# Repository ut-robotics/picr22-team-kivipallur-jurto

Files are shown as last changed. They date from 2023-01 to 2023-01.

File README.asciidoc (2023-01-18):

# Kivipallur-Jurto

Team members: +
Artur Reitalu +
Kristjan Madis Kask +
Kaspar Tamm +
Priit Teelahk +

== Fusion 360 Kivipallur Jürto
https://a360.co/3hoEI0K

== External links
Fusion 360 CAD - https://www.autodesk.com/products/fusion-360/overview?term=1-YEAR&tab=subscription +
Remmina - https://remmina.org/ +
Altium PCB Design - https://www.altium.com/ +
VNC Viewer/Server - https://www.realvnc.com/en/connect/download/viewer/ +
OpenSSH - https://www.openssh.com/ +

# Electronics
Compared to the beginning of the course, we reduced the electronics to a smaller size. On the new mainboard motor drivers and control logic are combined to one PCB. The new board has the option of adding more motors to add more functionality to the robot. It is easier to manage cables on the new board

The first fix to do is to add LEDs to the motor drivers. Another improvement is to buy new and better handling motor drivers for the course.

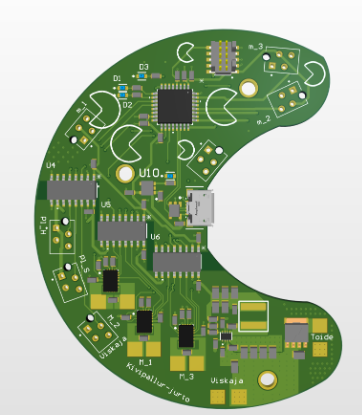
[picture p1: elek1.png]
Board1


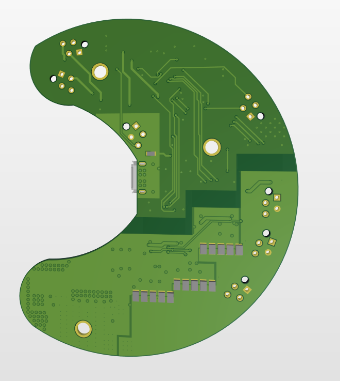
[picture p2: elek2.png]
Board2


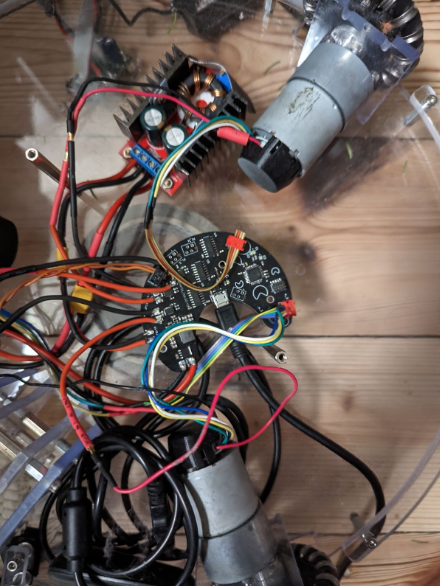
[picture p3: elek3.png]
Board3


# Mechanics

3d-printed battery and alarm holders for the robot for better fit and alarm stability. To add a little character to our robot, we added 3d-printed Kivipallur Jürto face to the camera holder. We also added some borders to sides and back to ensure that the ball will not get stuck outside or inside of the robot. We created 3d-printed borders to thrower, that guide the ball correctly. Moved most of the cables inside of the robot. +
Our ball thrower has a fixed throwing angle of 60 degrees. Distance between thrower sides is 42 mm, The distance between motor and ball slider ramps is 35 mm and the distance from motor to the ground is 38 mm. The sliders have cutouts for support and stability, as they sit on the bottom plate. +
Photos of our robot. +

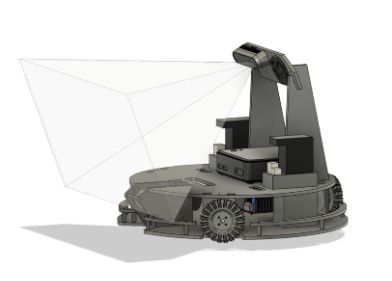
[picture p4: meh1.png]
robot1


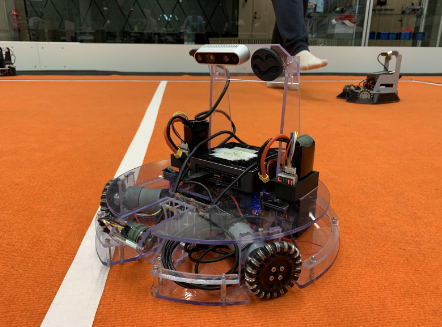
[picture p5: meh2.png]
robot2


Significant improvements can be achieved with smaller bottom and top plates. The robot did not do great in corners because of its big dimensions. Thrower clearance should be higher, because it would get stuck on some uneven surfaces. It’s more efficient to design the ball thrower with a ball holder and changeable angle, rather than a simple one. Otherwise everything worked perfectly and our robot was an improvement from the previous one. 

# Software

## Used libraries:

### OpenCV - https://opencv.org/ +
	Opencv is used for the image processing functions and object detection through contours.
  
### NumPy - https://numpy.org/ +
	Numpy allowed us to have and use more complex array processing functions for line detection.
  
### Xbox360controller - https://pypi.org/project/xbox360controller/ +
	Xbox360controller library was used solely for reading Xbox 360 controller inputs.

### Numba - https://numba.pydata.org/ +
	From the Numba library we used the JIT functions,which allowed us to speed up nested loops.

### WebSocket(Client) - https://pypi.org/project/websocket-client/ +
	Websocket client was used to actually connect to the referee server.

### Pyserial - https://pypi.org/project/pyserial/ +
	Pyserial was used to comfortably receive and send commands to the microprocessor which controlled the motors.

### Pyrealsense2 - https://pypi.org/project/pyrealsense2/ +
	Pyrealsense2 gave us the tools needed to use the camera feed from our intel realsense camera to its full potential.

### Multiprocessing - https://docs.python.org/3/library/multiprocessing.html +
	Multiprocessing is used as an alternative for multithreading, since it is supposed to be more effective.
	
### Pickle and segment + 
	Pickle and segment libraries were also used but they came with the bootcamp code, and pickle serialized objects and segment made color thresholding easier.

## Code structure

There were 4 main components in our code: +

* state machine
* referee listener
* omnimotion processor
* image processor

The state machine cycled through certain states (which are listed below), it was basically the coordinator on which functions to run and what to do with certain data from image processor. +

Referee listener was responsible for connecting to the referee server and constantly checking if there were new messages to forward to the state machine for it to change states and/or update basket color. +

OmniMotion processor converted basic forward and side ways movement in meters per second to correct maiboard units for the motors. +

Image processor is the component which analyzed camera frames and converted that info into ball, basket and line detetction

[horizontal]
Spin:: rotates to find a ball after about 1000 degrees of turning it goes into Enemy_basket_spin, if it found a ball before the goes into drive state.
Drive:: drives towards a found ball and stops after getting to certain range and goes into orbit state, if ball is lost during it goes back to spin state.
Orbit:: starts looking for the target basket while keeping the ball at the center of its camera(orbiting around ball), if ball is found goes into throw state, if ball is lost goes back into spin state.
Throw:: final lineup of ball and basket and starts the throw function, if ball is lost during this time goes back into spin state.
Controller:: if a connected controllers takeover button is pressed robot becomes controllable by controller until relinquish button is pressed.
Enemy_basket_spin:: state similar to spin but for the enemy basket, if found goes into enemy_basket_approach.
Enemy_basket_approach:: state to approach an enemy basket until a certain distance, if distance is reached goes back into spin state.

## Game logic
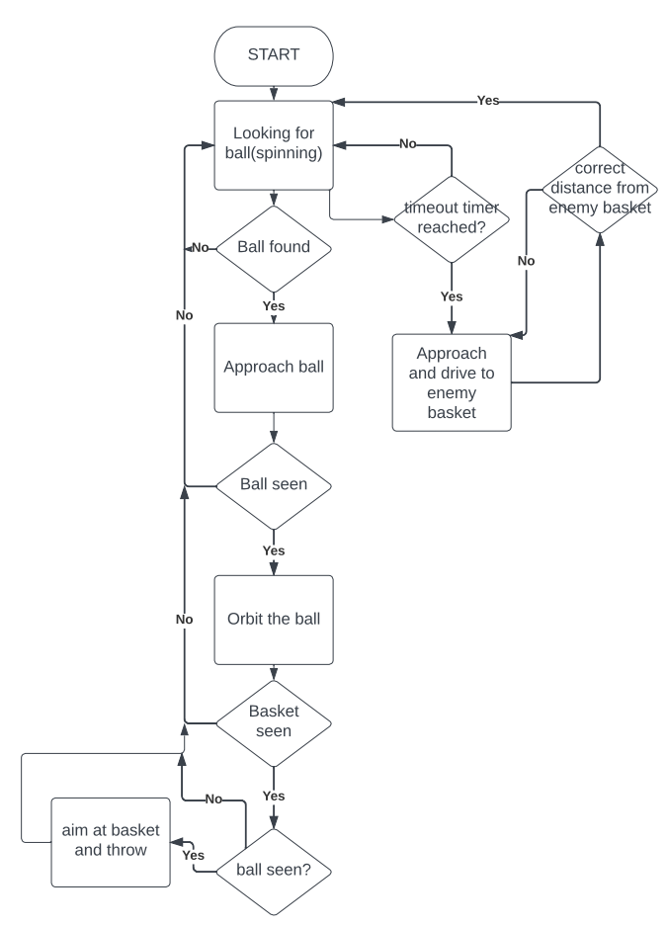
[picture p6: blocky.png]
blocky


## The Good, Bad and the ugly things i would change

### The GOOD +

I would say that the good things in our code were: numba jit which sped up our image processor and upped our frame rate by 10, controller integration which enabled our code to be able to be run without a referee server available and relatively more compact main.py then most.
	
### the BAD and the ugly i would change +

The worst thing about our code is that we don't measure our distance from object other than the basket which causes us to crash into other robots and the baskets backboard. Another bad thing is that our thrower speed calculation was linear which made it hard to throw in the balls. So i would change the depth camera usage to map out certain object if they are too close and execute countermeasures, and also remeasure our throwing distances and speeds.

# Personal comments

### Kaspar +
I worked on electronics design and assembly and wrote firmware for new electronics. I learned to use the Altium designer and STM32CubeIDE software. Next time I would do better to fix the schematic first before I start working on the PCB board. The collection of course materials is total chaos. The organization of the course has not been thought through. Next year's students, ask for advice from those who have passed already. Instructors must develop communication skills and the course schedule must be established before the course

### Artur +
I worked on the code together with Priit. I improved my code writing skills in python and also learnt about time management. Next time I would try to not reinvent the wheel (make everything by ourselves from scratch), but instead try to use more of what was available and already given to us (previous year’s code, instructors’ help, other teams’ help and their code examples). +
What I liked about the course was that it’s the only course (for us thus far at least) where you can earn money and you have creative freedom. +
What I did not like about the course was the lack of help, we got stuck on different tasks so often and it was super easy to burn out. We often just tried to fix one bug for several hours while with the instructors’ help it took only like 10 minutes to fix. The problem was that the instructors were available for only 2 lessons per week and then everybody needed their help, so there was a queue, who gets to ask them. Also the bi-weekly progress reports were extremely unnecessary and annoying in my opinion, as they just took away 25% of the sessions in which we could ask for the instructors’ help, instead we just had to watch and wait to get points. I don’t feel like it was motivating to move forward or make progress, but instead to just slow us down. +
Suggestion for next year’s students: Start early and don’t be scared to ask for help and use what has already been done for you. +
Suggestions for instructors: I understand that the current instructors work elsewhere and this course is like a part time job for them, but the students could really use more face-to-face consultations as slack communication is not very efficient and the in-person lessons always have such long queues to ask a question. + Maybe one more in-person lesson per week would ease the problem. +

### Madis +
I worked on the mechanics part of the robot. I learned to use Fusion 360 Autodesk software and how to design a functional robot from scratch. Learned how to use a mill and lathe. Next time I would look over my design a few more times to discover some mistakes I made. In this course I liked the idea of making all parts of the robot ourselves and getting a real functioning result. I didn’t like that sometimes I couldn’t continue my work, because I had to wait for supervision or the devices I had to use were in use. For future students I recommend starting early with everything and thoroughly thinking it through. For instructors I suggest to communicate more on slack, even if it's not so important, for example, if you haven’t supervised the work yet, but plan to do it in the next hours or day. It would be good to know all the issues right away, not each one with next feedback.

### Priit +
I worked together with Artur on the programmingof the robot. I learnt that cooperating with others while writing code is not always the best way, since we had many inconsistencies and problems. Next time i would definetly set out certain parts of the code i am responsible for and the other parts that my teammate is responsible for. The worst thing about the course was definetly the lack of lessons weekly which of some were completely gone for the progress presentation which actually dwarfed our progress i would say. Everything else in the course was great. Suggestions for other student would definetly be that try to complete the code and the robot by the 1st of December or even earlier, since building the new robot brings alot of new variables which could absolutely take all of your time away.
The instructors were very friendly and knowledgeable. There were some weird rules about formatting weekly reports, but other then that i have no personal quarrels.

== Blog

=== Sunday 2022-09-04

*Kaspar:* Soldered mainboard.  (2h) +
*Madis:* Assembled test robot. (1h) +

=== Wednesday 2022-09-07

*Priit:* Established a VNC Connection.  (2h) +
*Artur:* Helped with the VNC Connection.  (2h) +

=== Thursday 2022-09-08

*Kaspar:* Added heatshrink to cables. Connected a second powerswitch, which was missing.  (1.5h) +
*Priit:* Established communication with the mainboard.  (3.5h) +
*Artur:* Helped with Establishing a connection with the mainboard.  (3.5h) +

=== Monday 2022-09-12

*Madis:* Started designing the thrower. (5h) +
*Priit:* Attempted to establish a ssh connection, but didn t have much luck.  (2h) +
*Artur:* Also tried to get the ssh working to no avail.  (3.5h) +
*Kaspar:* Was writing an Estonian more throrough blog.  (1.5h) +

=== Thursday 2022-09-15

*Madis:* Finished designing the thrower. (5h) +
*Priit:* Got ssh working  (2h) +
*Artur:* Helped and celebrated getting ssh working.  (2h) +
*Kaspar:* Started doing the presentation.  (1.5h) +

=== Monday 2022-09-19

*Everyone except Madis:* Presented the presentation and listened to other teams. (3h) +

=== Thursday 2022-09-22

*Priit:* successfully opened the camera and tried different ways of detecting the balls. (4h) +
*Artur:* finsished the ball detection and we settled for the conture route (3h) +
*Kaspar:* Got Altium working and familiarised himself with the different components we could use.  (1.5h) +
*Madis:* Started with CAM, but ran into some problems with arrange (1h) +

=== Saturday 2022-09-24
*Madis:* Finished Fusion 360 CAM and waiting for supervision. (2h) +

=== Monday 2022-09-26

*Priit:* Helped with researching the code and main ball mover and carrier. (2h) +
*Artur:* Polished our ball detection software. Started developing the moving based on the closest balls x coordinate. (2h) +
*Kaspar:* Updated Project manager excel file, attached the NUC with screws to the test robot. Also photographed our accomplishments.  (2h) +

=== Wednesday 2022-09-28

*Artur:* Worked on robot movement. (2h) +

=== Thursday 2022-09-29
*Priit:* Broke the VNC Viewer tried different programs, but ended up back at VNC Viewer. (4h) +
*Kaspar:* Assisted with research on VNC Viewers. Worked on presentation slides, charged lipo batteries  (2h) +

=== Sunday 2022-10-02
*Priit:* reviewed the slides. (1h) +
*Kaspar:* reviewed the slides. (1h) +
*Artur:* reviewed the slides. (1h) +
*Madis:* reviewed the slides. (1h) +

=== Monday 2022-10-03
*Madis:* Resolved 2D Pocket and Contour issues with Fusion 360 CAM. Got positive feedback and milled the details. Presented the project status. (5h) +
*Priit:* Presented the project status. (1h) +
*Kaspar:* Presented the project status. (1h) +
*Artur:* Presented the project status. (1h) +

=== Thursday 2022-10-6
*Priit:* coded an alpha version of the code to track and follow the ball. (4h) +
*Artur:* helped to code and test the track and follow code.(2h) +
*Madis:* Modified robot and thrower, finally assembled thrower as well. (3h) +
*Kaspar:* Looking pcb components for Altium. (2h) + 

=== Friday 2022-10-7
*Kaspar:* Worked on motor driver and controller pcb schematic. (7h) +

=== Monday 2022-10-10
*Artur:* Worked on the robot motion program. (3h) +

=== Thursday 2022-10-13
*Priit:* Worked on the robot motion program and filmed robot moving in the field. (3h) +
*Kaspar:* Worked on slides and project plan, helped Priit debug the motion program. (3h) + 
*Madis:* Worked on the robot's wheel design. (3h) +

=== Sunday 2022-10-16
*Priit:* reviewed the slides. (1h) +
*Kaspar:* reviewed the slides. (1h) +
*Artur:* reviewed the slides. (1h) +
*Madis:* reviewed the slides. (1h) +

=== Monday 2022-10-17
*Priit:* Presented the project status. Did some coding. (4h) +
*Kaspar:* Presented the project status. Prepared the robot for the test robot presentation. (4h) +
*Artur:* Presented the project status. Did some coding. (4h) +
*Madis:* Presented the project status. Prepared the robot for the test robot presentation. (4h) +

=== Thursday 2022-10-20
*Madis:* Finished designing omniwheels and waiting for feedback. (4h) +

=== Friday 2022-10-21
*Madis:* Designed motor mounts and created assembly with omniwheel, motor holder and motor. (2h) +
*Kaspar:* Worked on motor driver and controller pcb schematic. (4h) +

=== Sunday 2022-10-23
*Artur:* Worked on the movement and image processing parts of the code. (3h) +
*Madis:* Fixed issues with motor mounts. (1h) +
*Kaspar:* Worked on motor driver and controller pcb schematic. (8h) +

=== Monday 2022-10-24
*Madis:* Used lathe to make three aluminum wheel-motor mounts. Next step is to clean them and drill holes. (4h) +
*Artur:* Improved our state machine code. (3h) +
*Priit:* Did some coding. (2h) +
*Kaspar:* Helped Priit with coding. (2h) +

=== Wednesday 2022-10-26
*Priit:* Struggled with classes and serial. (5h) +
*Madis:* Finished wheel-motor mounts. (2h) +
*Kaspar:* Experimented with the robot's ball throwing ability. (1h)+

=== Thursday 2022-10-27
*Priit:* Got the serial working and ironed out classes issue. (2h) +
*Artur:* Helped with debugging our issues. (2h) +

=== Friday 2022-10-28
*Priit:* Implemented primitive orbit and throwing functions. (4h) +
*Kaspar:* Worked on motor driver and controller pcb schematic. (4h) +
*Madis:* Started with camera holder design (2h) +

=== Saturday 2022-10-29
*Priit:* Improved orbit function. Also implemented depth camera distance. Fixed bugs (2h) +
*Kaspar:* Worked on motor driver and controller pcb schematic. (4h) +

=== Sunday 2022-10-30
*Priit:* reviewed the slides. (1h) +
*Madis:* reviewed the slides. (1h) +
*Artur:* reviewed the slides. (1h) +
*Kaspar:* reviewed the slides.Fixed feedback points and started pcb design (6h) +

=== Monday 2022-10-31
*Priit:* Presented the project status. (2h) +
*Kaspar:* Presented the project status. (2h) +
*Artur:* Presented the project status. (2h) +
*Madis:* Presented the project status. (2h) +

=== Thursday 2022-11-03
*Madis:* Designed new thrower. (3h) +
*Priit:* Developed a badly hardcoded throwing code. (3h) +
*Artur:* Worked on the robot program. (3h) +

=== Friday 2022-11-04
*Madis:* Started with new robot design (3h) +
*Kaspar:* Worked on pcb schematic and implemented suggested fixes (4h) +

=== Saturday 2022-11-05
*Kaspar:* Worked on pcb schematic and implemented suggested fixes (5h) +

=== Sunday 2022-11-06
*Madis:* Designed new robot upper plate and started to assemble new robot in Autocad (2h) +
*Kaspar:* Worked on pcb schematic and implemented suggested fixes (4h) +

=== Monday 2022-11-07
*Priit:* Fixed the hardcoded throwing code and added plastic fangs to help ball alignment (2h) +
*Kaspar:* Helped test the robot's ball throwing (2h) +
*Artur:* Improved new code. (2h) +

=== Tuesday 2022-11-08
*Madis:* Designed new robot. Added borders to bottom plate. (2h) +

=== Thursday 2022-11-10
*Priit:* Participated in the first test competition (5h) +
*Madis:* Participated in the first test competition (5h) +
*Artur:* Participated in the first test competition (5h) +
*Kaspar:* Participated in the first test competition (5h) +

=== Friday 2022-11-11
*Kaspar:* Fixed feedback points and started pcb design (3h) +

=== Saturday 2022-11-12
*Kaspar:* Received schematic feedback and finalized the new component placement (4h)

=== Sunday 2022-11-13
*Priit:* reviewed the slides. (1h) +
*Madis:* reviewed the slides. (1h) +
*Artur:* reviewed the slides. (1h) +
*Kaspar:* reviewed the slides. Improved component placement (4h) +

=== Monday 2022-11-14
*Priit:* presented progress (2h) +
*Madis:* presented progress (2h) +
*Artur:* presented progress (2h) +
*Kaspar:* presented progress (2h) +

=== Thursday 2022-11-17
*Priit:* Worked on remote control (2h) +
*Madis:* Worked on the robot design (2h) +
*Artur:* Worked on remote control (2h) +
*Kaspar:* Worked on pcb the design (2h) +

=== Saturday 2022-11-19
*Kaspar:* Received schematic feedback and Worked on pcb the design (5h) +

=== Monday 2022-11-21
*Madis:* Designed new robot. Need to add NUC (4h) +
*Kaspar:* Received schematic feedback and Worked on pcb the design (4h) +
*Priit:* Worked on the ref commands (3h) +
*Artur:* Worked on the ref commands (3h) +

=== Tuesday 2022-11-22
*Madis:* Finished Designing new robot. Waiting for feedback (2h) +

=== Wednesday 2022-11-23
*Kaspar:* Received schematic feedback and Worked on pcb the design (4h) +
*Priit:* prepared the robot for the test competition (3h) +
*Artur:* prepared the robot for the test competition (3h) +

=== Thursday 2022-11-24
*Priit:* Participated in the second test competition (5h) +
*Madis:* Participated in the second test competition (2h) +
*Artur:* Participated in the second test competition (5h) +

=== Friday 2022-11-25
*Kaspar:* Received schematic feedback and Worked on pcb design (2h) +

=== Saturday 2022-11-26
*Kaspar:* Prepared the pcb files to order the board (1h) +

=== Sunday 2022-11-27
*Priit:* reviewed the slides. (1h) +
*Madis:* reviewed the slides. (1h) +
*Artur:* reviewed the slides. (1h) +
*Kaspar:* reviewed the slides. (1h) +

=== Monday 2022-11-28
*Madis:* Presented progress (2h) +
*Kaspar:* Presented progress (2h) +

=== Wednesday 2022-11-30
*Madis:* 3D printed omni wheel and battery holder for testing (2h) +
*Priit:* Learned how to use github encryption keys (1h) +

=== Thursday 2022-12-01
*Madis:* Created CAM for milling new robot. Got feedback and milled new robot (5h) +
*Priit:* Added code for controller integration (4h) +

=== Sunday 2022-12-04
*Kaspar:* Worked on firmware (2h) +

=== Monday 2022-12-05
*Madis:* Assembled new robot chassis. Need to 3D print one more omni wheel. (4h) +
*Priit:* fixed issues with code (3h) +
*Kaspar:* Worked on firmware  (2h) +
  
=== Wednesday 2022-12-07
*Priit:* tested code on new robot, and tried coding firmware (6h) +
*Artur:* tested code on new robot, and tried coding firmware (6h) +
*Madis:* Assembled new robot (3h) +
*Kaspar:* Soldered our electronics (14h) +

=== Thursday 2022-12-08
*Priit:* tried writing a patrol function and wrote line detection kinda also participated in test competition (8h) +
*Madis:* fixed robot wheel and camera mount also participated in test competition (4h) +
*Artur:* thresholded and helped debugging and fix code also participated in test competition (5h) +
*Kaspar:* Added 3d printed electronics protection shell (3h) +

=== Saturday 2022-12-10
*Kaspar:* Worked on firmware  (5h) +

=== Sunday 2022-12-11
*Priit:* reviewed the slides. (1h) +
*Madis:* reviewed the slides. (1h) +
*Artur:* reviewed the slides. (1h) +
*Kaspar:* reviewed the slides and Worked on firmware . (3h) +

=== Monday 2022-12-12
*Priit:* optimized robot movement (5h) +
*Madis:* fixed robot thrower intake problems (5h) +
*Kaspar:* debugged our firmware (5h) +
*Artur:* helped with coding (2h) +

=== Wednesday 2022-12-14
*Madis:* Designed thrower with changeable throwing angle (4h) +

=== Thursday 2022-12-15
*Priit:* Improved the code (2h) +
*Madis:* fixed some problems with sheels and cleaned them (5h) +
*Kaspar:* Worked on electronics (15h) +
*Artur:* Worked on the code (2h) +

=== Friday 2022-12-16
*Priit:* Participated in DeltaX competition (4h) +
*Madis:* Participated in DeltaX competition (4h) +
*Kaspar:* Participated in DeltaX competition (4h) +
*Artur:* Participated in DeltaX competition (4h) +

=== Saturday 2022-12-17
*Priit:* Participated in course competition (4h) +
*Kaspar:* Participated in course competition (4h) +
*Artur:* Participated in course competition (4h) +

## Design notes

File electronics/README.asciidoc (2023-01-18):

= Kivipallur Jurto electronics documentation

== Kivipallur Jurto mainboard functionality

* Mainboard consists of 2 separate isolated schematics: 
** Logic schematic with is powered with USB source
** Motor drivers schematic is powered with lithium ion battery

* Communication between the mainboard STM32 controller and computer is through microUSB

* Mainboard is programmable with STLINK-V3 mainboard has for that Samtec connector

* Mainboard has 7 MicroMatch connectors: 
** 3 for movement motor encoders (m_1; m_2; m_3)
** 1 for Thrower motor (Viskaja)
** 1 for Throwing angle adjust servo motor (Pl_S)
** 1 for Ball holder servo motor (Pl_H)
** 1 for Ball sensor

* Mainboard has 2 voltage regulators 
** Logic schematic to turn 5V to 3.3V 
** Motor drivers schematic to turn 16V to 5V

* Mainboard has 3 drivers (DRV8243HQRXYRQ1) for controlling motors (M_1; M_2; M_3). With these drivers we can control 3 brushed DC motors at the same time

* Motor drivers input voltage is limited with capacitors that are connected to the drivers. Capacitors that are used have 25V rating, technically the maxium voltage is 25V. But the robot uses 4 cell lithium ion battery's that have voltage up to 16.8V. The current coming out of motor drivers is limited with resistors that are connected to the ITRIP pin and IPROPI pins
** ITRIP pin is connected with 47k resistor, that sets Voltage to 2.31V
** IPROPI pin is connected with 2.7k resistor, then the current is limited to 2.63A.

* Motor drivers are controlled through 1 PWM signals and one direction signal.

* Motor drivers need nSLEEP pulse to initialize

* Motor drivers SR pin for slew rate with 47k resistor. High slew rate is better for efficiency, but you have to be careful with slew rate configuration it has caused problems in previous years

* Motor drivers DRVOFF pin to put the driver on standby 

== Connector pinouts

=== Logic schematic

* (J7) Programmer connector
** pin 1 +3.3V
** pin 2 Debug SWDIO
** pin 3 GND
** pin 4 Debug SWCLIK
** pin 5 GND
** pin 6 not used
** pin 7 not used
** pin 8 not used
** pin 9 GND
** pin 10 Debug NRST

* (J8) Motor 1 encoder (m_1)
** pin 1 GND
** pin 2 +3.3V
** pin 3 Mikro-m1-en1
** pin 4 Micro-m1-en2

* (J10) Motor 2 encoder (m_2)
** pin 1 GND
** pin 2 +3.3V
** pin 3 Mikro-m2-en1
** pin 4 Micro-m2-en2

* (J12) Motor 3 encoder (m_3)
** pin 1 GND
** pin 2 +3.3V
** pin 3 Mikro-m3-en1
** pin 4 Micro-m3-en2

* (J13) Ball sensor
** pin 1 GND
** pin 2 +5V_USB
** pin 3 not used
** pin 4 LED_B2

=== Motor drivers schematic

* Lithium ion battery connection
** J16 is for + connection
** J17 is for - connection

* (J14) Thrower connector (Viskaja)
** pin 1 GND
** pin 2 Viskaja_Mootor
** pin 3 not used
** pin 3 not used

* (J9) Ball holder connector (Pl_H)
** pin 1 +5V
** pin 2 Palli_H
** pin 3 GND
** pin 4 not used

* (J11) Throwing angle connector (Pl_S)
** pin 1 +5V
** pin 2 Palli_S
** pin 3 GND
** pin 4 not used

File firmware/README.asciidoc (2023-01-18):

= Kivipallur Jurto firmware

== Data to mainbord

In order to be able to communicate between the computer and the mainbord. The speed values must be in the correct byte form.

Python speed send comand:

---- 
andmed = struct.pack('<hhhHBH', speed1, speed2, speed3, thrower_speed, disable_failsafe, 0xAAAA)
----

* h - speed1, speed2, speed3 are int16_t
* H - thrower_speed, disable_failsafe are uint16_t
* 0xAAAA don't change
* Thrower speed can be from 20 - 6000

== Kivipallur Jurto software does not support feedback

* Feedback was not neede for Kivipallur Jurtos software
* Kivipallur Jurtos firmware has feedback support

* To recieve data from mainboard, the python program has to read that from serial. After reding the data can be printed

* Mainboard returns feedback struct variables
** int16_t speed1
*** returns Motor1 feedback
** int16_t speed2
*** returns Motor2 feedback
** int16_t speed3
*** returns Motor3 feedback
** uint16_t delimiter
*** delimiter value 0xAAAA

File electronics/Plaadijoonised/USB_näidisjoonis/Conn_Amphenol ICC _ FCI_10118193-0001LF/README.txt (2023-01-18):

EE Concierge + Altium Library Install Instruction:

The following are the instructions for loading a library that was exported from EE Concierge into Altium.

The library will come as a zip file filled with all the necessary Altium data files required to load your EE Concierge parts into Altium. For every part there will be a pcb file, and a schematic file. There will also be an index file, a readme file, and finally the master library file itself. Do not try to open any of the individual part files, or the index file as they can't be loaded on their own.

Instead, to load a library you simply need to point Altium to this master library file named: 'EEConcierge.DbLib'. There are two ways to do this which we outline below. Whenever you need to load an updated version of your EE Concierge library the instructions are exactly the same. We've tagged the parts exports in such a way that Altium will overwrite and update any previously loaded parts as opposed to creating duplicates.

Method A:

1) Unzip the exported library
2) Double click on the file 'EEConcierge.DbLib'
3) Altium will open and load the library for you, you can now use your new components

Method B:

1) Unzip the exported library
2) Open Altium Designer
3) In the 'File' menu, click 'Open'
4) Browse to the unzipped library directory, select 'EEConcierge.DbLib' and click 'Open'

Altium will load the library, you can now use your new components
Part 10118193-0001LF (component id ec30cc09bb8fb2b7) experienced an error during datasheet export:
Traceback (most recent call last):
  File "/home/upverter/schematic-file-converter/upconvert/writer/altium/altium.py", line 406, in export_datasheet
    datasheets[datasheet_url] = self.save_datasheet(datasheet_url)
  File "/home/upverter/schematic-file-converter/upconvert/writer/altium/altium.py", line 300, in save_datasheet
    r.raise_for_status()
  File "/usr/lib/python2.7/dist-packages/requests/models.py", line 935, in raise_for_status
    raise HTTPError(http_error_msg, response=self)
HTTPError: 503 Server Error: Service Temporarily Unavailable for url: https://cdn.amphenol-icc.com/media/wysiwyg/files/drawing/10118193.pdf

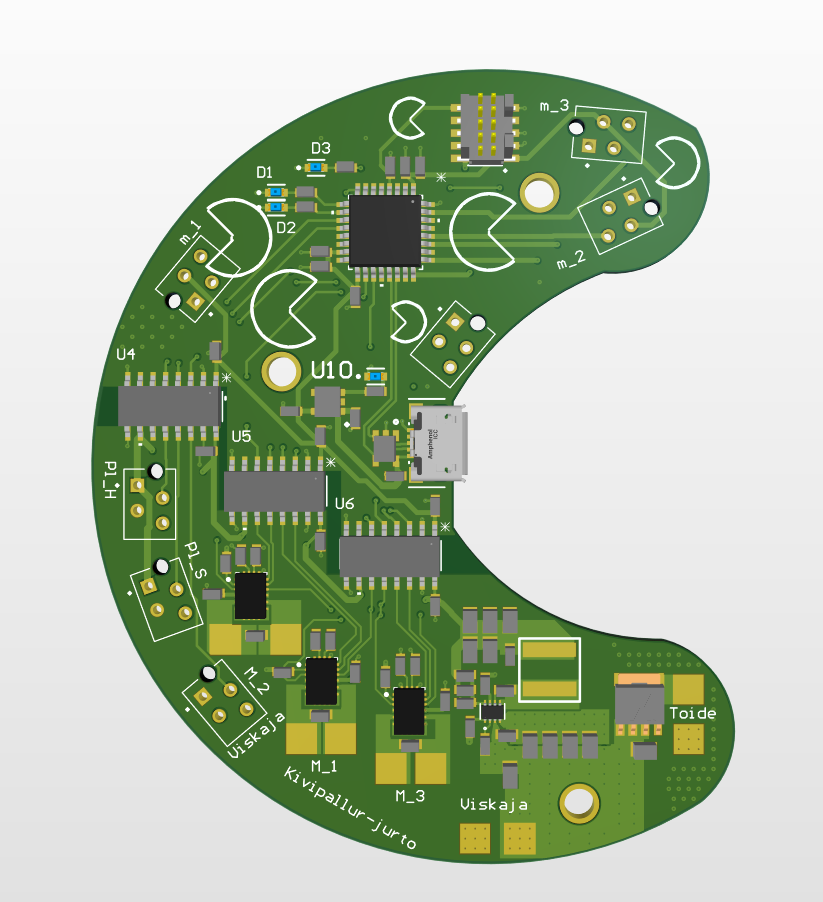
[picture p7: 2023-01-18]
electronics/PCB_png/Kivipallur_Jurto_PCB_front.png

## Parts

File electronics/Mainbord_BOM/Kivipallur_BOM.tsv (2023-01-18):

Name | Description | Designator | Quantity | Mouser | Farnell | TME
10uF | Capacitor 0805 | C1, C2, C3, C4, C5, C6, C7, C8, C9, C10, C11, C12, C13, C14, C15, C35, C36, C37, C38, C39, C40, C41, C42, C43, C44, C53 | 26 | 581-08053D106KAT2A | 2346927 | C2012X5R1E106KAB
0.1uF | Capacitor 0603 | C16, C17, C18 | 3 | 187-CL10B104KA8NNNL | 3764197 | 06033C104K4T2A
100nF | Capacitor 0603 | C19, C20, C21, C22, C23, C24, C25, C26, C27, C29, C30, C31, C32, C45, C46, C47, C49 | 17 | 187-CL10B104KA8NNNL | 2332586 | 0603B104J500CT
4.7uF | Capacitor 0603 | C28, C33, C34 | 3 | 581-0603YW475KAT2A | 2211173 | 0603X475K100CT
10pF | Capacitor 0603 | C48 | 1 | 80-C0603C100J3HACTU | 3366207 | 06031A100CAT2A
1uF | Capacitor 0603 | C50, C51, C52 | 3 | 581-06035C105KAT2A | 3881046 | CL10A105KA8NNNC
LTST-C191TBKT | LED BLUE CLEAR CHIP SMD | D1, D2, D3, D4 | 4 | 859-LTST-C191TBKT | 1610883 | LTST-C191TBKT
FTSH-105-01-L-DV-K | Connector Header Surface Mount 10 position 0.050" (1.27mm) | J7 | 1 | 200-FTSH10501LDVK | 3550960 | NOT IN STOCK
215079-4 | 4 Position Receptacle Connector Through Hole | J8, J9, J10, J11, J12, J13, J14 | 7 | 571-215079-4 | 1772996 | AMP-7-215079-4
10118193-0001LF | Micro USB Type B | J15 | 1 | 649-10118193-0001LF | 2751675 | 10118193-0001LF/C
SRP6060FA-5R6M | Power Inductors | L1 | 1 | 652-SRP6060FA-5R6M | 2901832 | NOT IN STOCK
BUK6Y10-30P | Reverse Voltage protection | Q1 | 1 | 771-BUK6Y10-30PX | 3438512 | BUK6Y10-30PX
2.7k | Resistor 0603 | R1, R2, R3 | 3 | 652-CR0603-FX2701ELF | 9238530 | HP03-2K71%
47k | Resistor 0603 | R4, R5, R6, R7, R8, R9, R16 | 7 | 652-CR0603FX-4702ELF | 9238689 | CRGCQ0603J47K
3.3k | Resistor 0603 | R10, R11, R12, R17 | 4 | 667-ERJ-3EKF3301V | 9238549 | ARG0603-3K3-0.5%
10k | Resistor 0603 | R13 | 1 | 603-RT0603FRE0710KL | 2073356 | CRGP0603F10K
53.6k | Resistor 0603 | R14 | 1 | 667-ERJ-3EKF5362V | 3495876 | ERA3AEB5362V
10.2k | Resistor 0603 | R15 | 1 | 603-RT0603FRE0710K2L | 3495721 | ERJ3EKF1022V
PDRV8243HRXYQ1 | Motor driver | U1, U2, U3 | 3 | 595-DRV8243HQRXYRQ1 | NOT IN STOCK | NOT IN STOCK
MAX14930DASE+ | 4 channel isolator | U4, U5, U6 | 3 | 700-MAX14930DASE+ | 3257451 | NOT IN STOCK
STM32G441KBT3 | Microcontroller | U7 | 1 | 511-STM32G431KBT6 | 3132405 | NOT IN STOCK
XTPS62933DRLR | Motor driver voltage regulator | U8 | 1 | 595-TPS62933DRLR | NOT IN STOCK | NOT IN STOCK
CM1223-03SO TVS diode array | USB protection | U9 | 1 | 748-CM1223-02SO | 3607672 | CM1223-02SO
NCP164CSN330T1G | Logic voltage regulator | U10 | 1 | 863-NCP164CSN330T1G | 3367831 | NCP164CSN330T1G

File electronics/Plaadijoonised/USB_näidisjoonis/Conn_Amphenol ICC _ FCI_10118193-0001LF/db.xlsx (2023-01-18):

Library Ref | Library Path | Datasheet Path | Automotive | ComponentLink1Description | ComponentLink1URL | ComponentLink2Description | ComponentLink2URL | Conn Orientation | Contact Material | Current Rating | Description | Digikey Description | Digikey Part Number | Footprint Path | Footprint Ref | Height | Is Female | Lead Free | Manufacturer | Mouser Description | Mouser Part Number | Number Of Contacts | Package | Part Number | Pitch | RoHS | Shielding | Supplier 1 | Supplier 2 | Supplier Part Number 1 | Supplier Part Number 2 | Symbol Hash | Temperature | Temperature Range High | Temperature Range Low | Usb Standard | Verification Version | Voltage Rating | helpURL
10118193-0001LF | parts/Conn_Amphenol_ICC_-_FCI_10118193-0001LF_eec.SchLib | datasheets/Conn_Amphenol_ICC_-_FCI_10118193-0001LF_eec.pdf | No | Upverter | https://upverter.com/part/id/ec30cc09bb8fb2b7/ | Datasheet | https://cdn.amphenol-icc.com/media/wysiwyg/files/drawing/10118193.pdf | Right Angle | Gold,Nickel | 1.8A | USB - micro B USB 2.0 Receptacle Connector 5 Position Surface Mount, Right Angle; Through Hole | CONN RCPT USB2.0 MICRO B SMD R/A | 609-4616-1-ND | parts/Conn_Amphenol_ICC_-_FCI_10118193-0001LF_eec_MFG.PcbLib | Amphenol_ICC_-_FCI_0_MFG | 3mm | yes | Yes | Amphenol ICC / FCI | Conn Micro USB Type B RCP 5 POS 0.65mm Solder RA SMD 5 Terminal 1 Port T/R | 649-10118193-0001LF | 5 | 0 | 10118193-0001LF | 0.65mm | TRUE | true | Digi-Key | Mouser | 609-4616-1-ND | 649-10118193-0001LF | fccd9f5d169b9690fa774be72a27040905a04abf6ee7ab2f05b972d6146d7061 | -55°C to +85°C | +85°C | -55°C | USB 2.0 | 0.0.0.3 | 100V | https://upverter.com/part/id/ec30cc09bb8fb2b7/

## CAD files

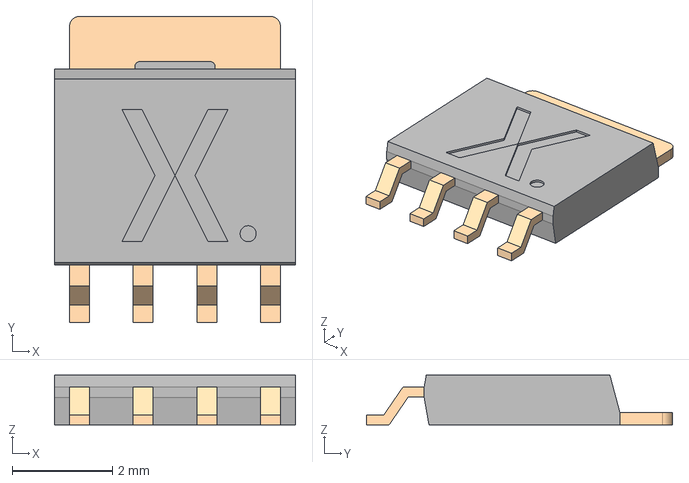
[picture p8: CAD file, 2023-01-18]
electronics/Plaadijoonised/BUK6Y10-30P/SOT669.step
4.81 x 6.11 x 0.998 mm

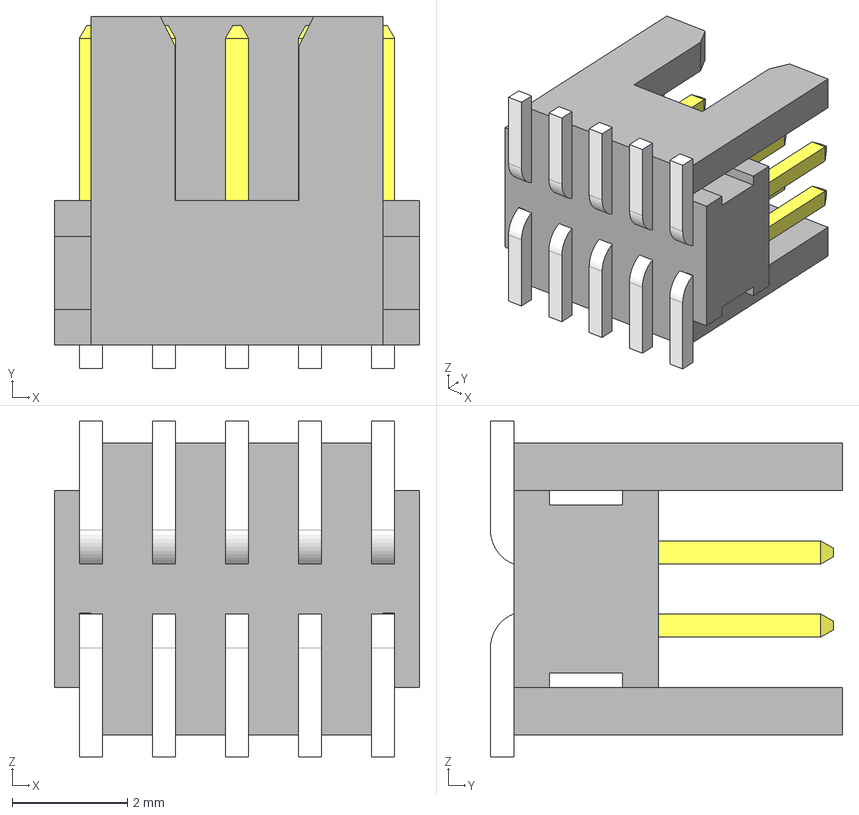
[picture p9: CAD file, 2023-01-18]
electronics/Plaadijoonised/FTSH-105/FTSH-105-01-L-DV-K.stp
6.35 x 6.12 x 5.84 mm
FTSH-105-01-L-DV-K_pins2
FTSH-105-01-L-DV-K_pins1
FTSH-105-01-L-DV-K_body

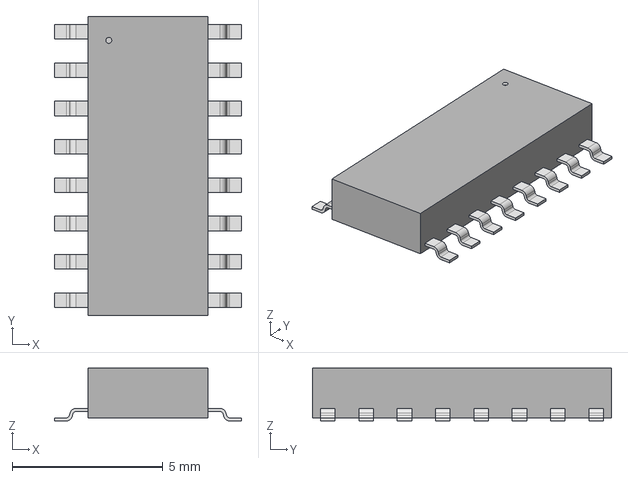
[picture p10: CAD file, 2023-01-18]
electronics/Plaadijoonised/isolaator/MAX14930DASE+/21-0041_S16+1_MXM.step
6.20 x 9.91 x 1.75 mm

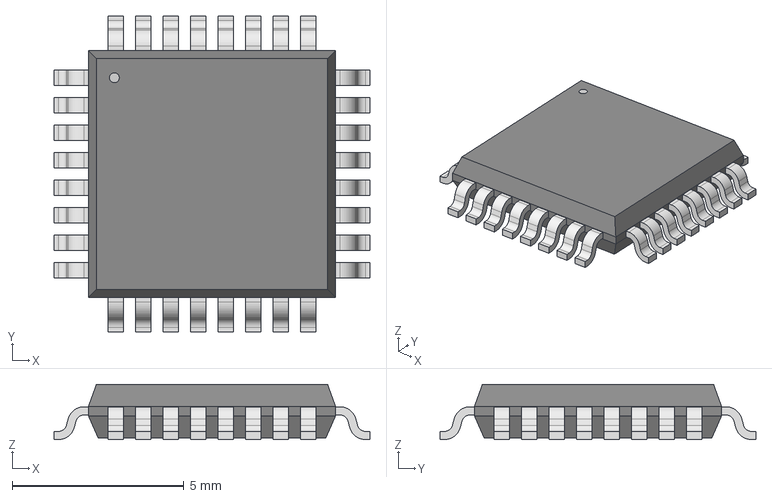
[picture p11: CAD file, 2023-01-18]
electronics/Plaadijoonised/Microkontroller/STM32G441KB/LQFP32_7X7_STM.step
9.19 x 9.19 x 1.60 mm

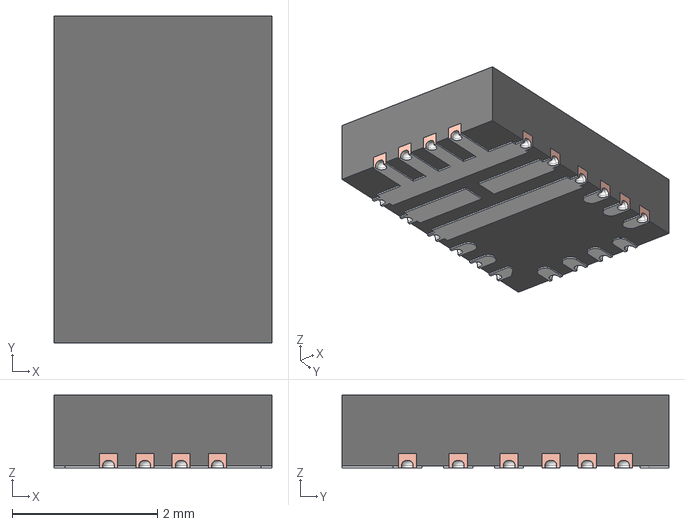
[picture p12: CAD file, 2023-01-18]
electronics/Plaadijoonised/Mootori kontroller/PDRV8243HRXYQ1/RXY0014A.stp
3.00 x 4.50 x 1.00 mm
FRAME
MOLD

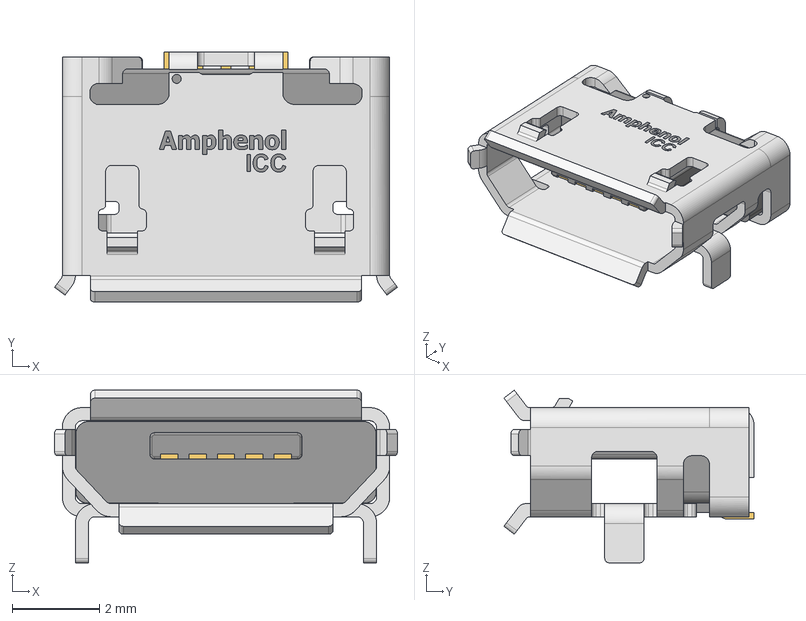
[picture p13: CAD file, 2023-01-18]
electronics/Plaadijoonised/USB_näidisjoonis/Conn_Amphenol ICC _ FCI_10118193-0001LF/parts/Conn_Amphenol_ICC_-_FCI_10118193-0001LF_eec.STEP
7.86 x 5.73 x 3.96 mm
int
pins
logo

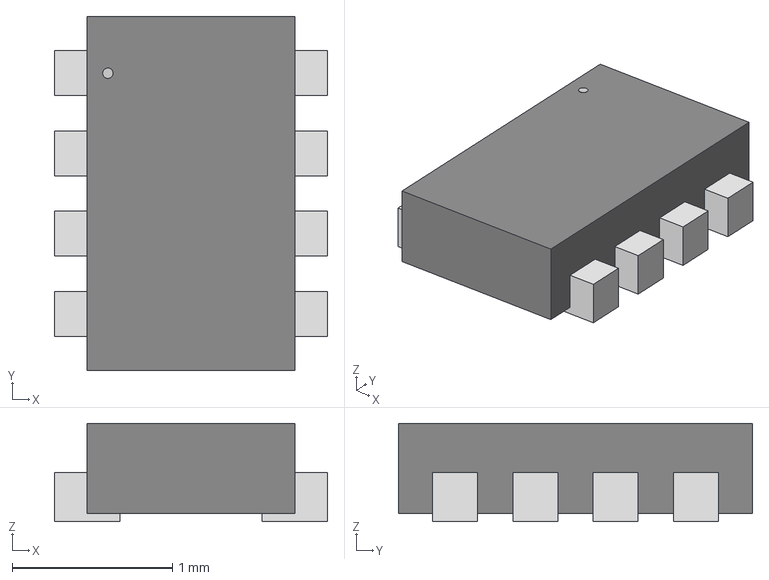
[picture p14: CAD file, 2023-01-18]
electronics/Plaadijoonised/XTPS62933DRLR/ul_XTPS62933DRLR/AltiumDesigner/2022-11-05_18-56-45/SOT_33DRLR_TEX.step
1.70 x 2.21 x 0.612 mm

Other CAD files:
electronics/Plaadijoonised/isolaator/ul_MAX14930DASE-/2022-10-07_18-44-25/STEP/21-0041_S161_MXM.step
electronics/Plaadijoonised/isolaator/ul_MAX14930DASE-/2022-10-28_20-59-48/STEP/21-0041_S161_MXM.step
electronics/Plaadijoonised/isolaator/ul_MAX14930DASE-/AltiumDesigner/2022-10-28_20-59-46/21-0041_S16+1_MXM.step
electronics/Plaadijoonised/Microkontroller/ul_STM32G441KBT3/2022-10-07_21-08-16/STEP/LQFP32_7X7_STM.step
electronics/Plaadijoonised/Project Outputs for FTSH-105-XX-X-DV_2.0/FTSH-105-01-L-DV-K.stp

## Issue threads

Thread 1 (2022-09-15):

[Mechanics] Wrong material thickness

maidlam, 2022-09-15:
Material thickness for a 5mm PC sheet is actually 4.8mm

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

KMKgit, 2022-09-15:
resolved

Closed 2022-09-17.

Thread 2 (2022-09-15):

[Mechanics] Not clear where thrower motor cables run

maidlam, 2022-09-15:
From the current model it is unclear from where motor power cables run. Would be great if they can be found on the model, at least a representation of the cable exit area is needed.

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

Closed 2022-09-17.

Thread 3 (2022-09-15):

[Mechanics] Bolt holes missing in side walls

maidlam, 2022-09-15:
Holes for attaching the thrower to the chassis are missing.

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

KMKgit, 2022-09-15:
resolved

Closed 2022-09-17.

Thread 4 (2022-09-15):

[Mechanics] Thrower ramps interference with bottom plate

maidlam, 2022-09-15:
The ramps of the thrower interfere with the bottom plate.

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

One option might be to make a cutout so that the ramp fits over the plate.

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

KMKgit, 2022-09-15:
resolved

Closed 2022-09-17.

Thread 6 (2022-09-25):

[Mechanics] Issues with 2D Pocket

maidlam, 2022-09-25:
1. Increase Maximum Stepover under Passes.
2. Increase Maximum roughing Stepdown in Multiple Depths to 1 mm.
3. Change Stock to Leave settings.

Use the same settings as in the guide
https://ut-robotics.github.io/picr22-home/basketball_robot_guide/mechanics/cam.html#_pocket

KMKgit, 2022-10-03:
Resolved

Closed 2022-10-05.

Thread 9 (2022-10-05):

[Mechanics] disable "keep tool down"

Akustav, 2022-10-05:
The option "Keep Tool Down" sometimes can keep the tool down when changing contours. This can make the mill cut at jogging speed through material, creating issues. The issue spot is here:

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

This option should be disabled:

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

Closed 2022-10-12.

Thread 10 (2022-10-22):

[Mechanics] motor-wheel mount optimizations

Akustav, 2022-10-22:
You can make the mount smaller to make it simpler to create. You can make the mounting part shorter and also put the fastening hole in between the wheel mounting holes to avoid potential interference.

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

KMKgit, 2022-10-23:
Resolved. Reduced the length by 1mm. Cannot make it any shorter, otherwise the mounting screw wouldn't fit and it wouldn't be on the flattened part of the motor shaft.

Closed 2022-10-28.

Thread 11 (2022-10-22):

[Mechanics] add hole for shaft to omniwheel body

Akustav, 2022-10-22:
You can add a hole to the omni wheel body where the shaft can move into. Currently this is the most compact you can make the assembly:

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

with a hole, you can make it more compact:

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

KMKgit, 2022-10-23:
resolved

Closed 2022-10-28.

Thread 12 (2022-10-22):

[Mechanics] wrong hole size

Akustav, 2022-10-22:
The holes on the wheel-motor mount should be 2.5mm for threading:

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

KMKgit, 2022-10-23:
resolved

Closed 2022-10-28.

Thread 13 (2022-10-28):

[Mechanics] camera side legs cutouts

Akustav, 2022-10-28:
You have cutouts in the side panels for the camera mount. This can increase flex in the mount and make the camera vibrate more. Are they needed?

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

KMKgit, 2022-10-30:
It's not essential, but it helps with cable management. I can perhaps make one smaller cutout.

Akustav, 2022-11-05:
I suggest that to avoid excess vibrations and swaying.

Closed 2022-11-26.

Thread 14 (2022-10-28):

[Mechanics] wrong hole size in camera mount

Akustav, 2022-10-28:
Threaded holes should be 2.5mm:

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

KMKgit, 2022-11-22:
Resolved

Closed 2022-11-26.

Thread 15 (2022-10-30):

MCU pin assignement

ReikoR, 2022-10-30:
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

Did you use STM32CubeIDE for creating the pin assignment?
Based on the schematic I could not find pin assignment that would work.

For example pin PA2 and PA3 connect to timer 15 channels, but timer 15 does not have encoder mode.
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

Some more information on how to configure timers in STM32CubeIDE is on the firmware page:
https://ut-robotics.github.io/picr22-home/basketball_robot_guide/electronics/firmware.html

ReikoR, 2022-11-05:
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

Encoder signals are not connected correctly.

Something like this is one option:
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

Also motor driver PWM and direction signal ports have basically the same name as encoder signal nets:
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

Closed 2022-11-06.

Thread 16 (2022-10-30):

3.3V net name

ReikoR, 2022-10-30:
Some are named: `3,3V`
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

Some are named: `3.3V`:
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

ReikoR, 2022-11-05:
On MCU schematic (joonis2) `3.3V` is used:
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

On motor drivers and encoders schematic (joonis1) `+3.3V` is used:
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

Closed 2022-11-06.

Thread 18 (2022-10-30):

Multiple net names

ReikoR, 2022-10-30:
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

Power symbols define net name. Additional net name should not be added.

These problems can also be found with **Project -> Validate PCB Project**.

Closed 2022-11-05.

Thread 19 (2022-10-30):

Use more input and output capacitance for voltage regulators

ReikoR, 2022-10-30:
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

From [NCP164 datasheet](https://www.onsemi.com/pdf/datasheet/ncp164-d.pdf):
> **Input Decoupling (C<sub>IN</sub>)**
> It is recommended to connect at least 1 uF ceramic X5R or X7R capacitor between IN and GND pin of the device.

> **Output Decoupling (C<sub>OUT</sub>)**
> The device is designed to be stable with standard ceramics capacitors with values of 1 uF or greater.

NCV8730 regulator has the same problem.

Closed 2022-11-05.

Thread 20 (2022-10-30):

NCV8730ASN500T1G does not need feedback resistors

ReikoR, 2022-10-30:
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

NCV8730ASN500T1G has fixed output of 5V.

From [datasheet](https://www.onsemi.com/pdf/datasheet/ncv8730-d.pdf):
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

Closed 2022-11-06.

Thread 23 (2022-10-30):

DRV8243 VM pins need more capacitance

ReikoR, 2022-10-30:
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

More capacitance is needed during switching at driver's input (VM) to avoid voltage drop at the driver's output.
Around 50 uF might be fine. For example it's possible to use 5x 10 uF ceramic capacitors.

ReikoR, 2022-11-05:
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

100uF 25V+ 0805 capacitors do not exist or are not available.

100uF 25V+ ceramic capacitors in stock at Mouser:
https://www.mouser.ee/c/passive-components/capacitors/mlccs/multilayer-ceramic-capacitors-mlcc-smd-smt/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

ReikoR, 2022-11-06:
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

100 uF capacitors in 2220 package cost too much:
https://www.mouser.ee/ProductDetail/Murata-Electronics/KCM55WC71E107MH13L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

We already have bought 10uF 0805 capacitors. It's recommended to use about 5 of them for each driver.

Closed 2022-11-12.

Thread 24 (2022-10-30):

DRV8243 configuration pins

ReikoR, 2022-10-30:
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

1k resistors are not suitable as they are out of range of recommended values.
From [datasheet](https://ut-robotics.github.io/picr22-home/basketball_robot_guide/electronics/drv8243-q1_datasheet_2021-08.pdf):
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

ReikoR, 2022-11-05:
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

Connecting 100k resistor to SR pin sets the slew rate to the highest value:
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

This can't be read form the datasheet, but highest slew rate caused problems last year with motors not starting or rotating properly. Using slew rates of 23 or 28 V/usec worked fine.

ReikoR, 2022-11-06:
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

50k resistors are not very common. It's better to use 47k, which should also available in the lab.

It's not been tested whether it works or not, but slew rate of 38 V/usec is not too much smaller than 43 and might still cause problems.

Closed 2022-11-12.

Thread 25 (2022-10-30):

Motor driver output connectors missing

ReikoR, 2022-10-30:
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

I didn't find any connectors (simple SMD pads preferably) for motor driver outputs.

Motor driver outputs should not be connected together (with "Toide" net on the schematic).

ReikoR, 2022-11-05:
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

3x3_mm symbol does not have the pin rotated correctly.

There are 4 small white dots (only 2 are visible here) at the end of the pin where the wire needs to connect:
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

Closed 2022-11-06.

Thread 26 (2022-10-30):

Servo signals and power

ReikoR, 2022-10-30:
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

Are `Palli_H` and `Palli_S` servo PWM signals?

If they are, then 5V switching regulator would also be needed to power the servos, since linear regulators are inefficient for higher currents.

ReikoR, 2022-11-05:
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

NCV8730 regulator is only rated for 150 mA output current, which is not enough for servos. Linear regulators in general are inefficient for higher currents.

We have bought XTPS62933DRLR switching regulators and SRP6060FA-5R6M inductors for powering the servos:
https://ut-robotics.github.io/picr22-home/basketball_robot_guide/electronics/components.html

Texas Instruments Webench can be used to help with the design:
https://webench.ti.com/power-designer/switching-regulator?powerSupply=0

ReikoR, 2022-11-06:
1. RT pin should be left floating, connected to GND or to resistor.
\
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
\
From [TPS62933 datasheet](https://www.ti.com/lit/ds/symlink/tps62933.pdf?ts=1667748094702):
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

2. 130k and 22k feedback resistors set the output voltage to about 5.5V, not 5V.
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

ReikoR, 2022-11-12:
1. 100k RT resistor results in switching frequency of 225 kHz.
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
\
When using this frequency in https://webench.ti.com/power-designer/switching-regulator, it says:
_This design is not stable due phase margin either smaller than 35 or greater than 120._
\
Also lower switching frequency requires inductor with higher inductance.
\
Either lower resistor value needs to be used to set switching frequency higher or RT pin should be left unconnected to set frequency to 500 kHz.

2. Feedback resistors should be changed, not the power port value:
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
\
5.5V is too close to maximum recommended supply voltage for isolators.
From [datasheet](https://datasheets.maximintegrated.com/en/ds/MAX14130-MAX14932.pdf):
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

ReikoR, 2022-11-20:
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

100k and 22k feedback resistors set the output voltage to 4.436 V.

If you don't know how to select the resistor values, then see sections _9.3.4 Output Voltage Setting_ and _10.2.2.2 Output Voltage Resistors Selection_ in the [TPS62933 datasheet](https://www.ti.com/lit/ds/symlink/tps62933.pdf).

Closed 2022-11-22.

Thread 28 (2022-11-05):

[Mechanics] Use chassis to support internal ramp

Akustav, 2022-11-05:
This is not necessarily a issue but more of a suggestion. I think you can use the chassis to support the internal ramp as well. Maybe add a lip that rests on the chassis, like this:

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

Or cutouts from the bottom plate to support the ramps from the sides:

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

It is something to consider

KMKgit, 2022-11-08:
Resolved

Akustav, 2022-11-26:
If you add this lip, it is even more supported:

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

KMKgit, 2022-11-28:
resolved

Closed 2022-11-30.

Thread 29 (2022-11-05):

Add decoupling capacitors to each MCU power pin

ReikoR, 2022-11-05:
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

Each VDD/VDDA pin should have at least one 100nF capacitor.

ReikoR, 2022-11-06:
Capacitors should not be connected in series to 3.3V.

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

ReikoR, 2022-11-12:
Avoid having different units for same value components:
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

Also 100 nF capacitor per VDD/VDDA pin and one 4.7 uF capacitor would be enough.

Closed 2022-11-15.

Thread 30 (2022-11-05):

GND nets need to have different names

ReikoR, 2022-11-05:
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

If GND or power symbols in general have the same names then their connected together. Different names need to be used for MCU side and motor drivers side.

Closed 2022-11-06.

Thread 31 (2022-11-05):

Don't use metric grid on the schematic

ReikoR, 2022-11-05:
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

Industry standard unfortunately is 100 mil grid. All the symbols are designed for it. Using different grid can cause issues with things not aligning with each other.

On the PCB it's better to use metric grid.

Closed 2022-11-06.

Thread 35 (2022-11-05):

Make PCB smaller

ReikoR, 2022-11-05:
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

PCBs larger than 100 x 100 mm cost more:
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
https://cart.jlcpcb.com/quote?orderType=1&stencilLayer=4&stencilWidth=105&stencilLength=130&stencilCounts=5

For lowest cost the PCB should be smaller than 50 x 50 mm.

Closed 2022-11-27.

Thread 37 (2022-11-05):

Use smaller 100nF capacitors

ReikoR, 2022-11-05:
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

Smaller decoupling capacitors are easier to place. In the lab we have 100nF capacitors in 0603 package. We probably don't have them in any other sizes.

Closed 2022-11-12.

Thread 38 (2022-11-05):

Place decoupling capacitor as close as possible to power pins

ReikoR, 2022-11-05:
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

Connect with wide and short tracks. Longer tracks have more inductance, which decreases the usefulness of the capacitors.

ReikoR, 2022-11-15:
5V isolator capacitors can be placed closer.
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

Closed 2022-11-20.

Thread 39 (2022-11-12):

Use smaller LEDs

ReikoR, 2022-11-12:
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

In the lab we have LEDs in 0603 package.

ReikoR, 2022-11-15:
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

This is not a correct footprint to use.

I meant imperial 0603 (1608 metric) size.

You can try Manufacturing Part Search to find suitable components.
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

Closed 2022-11-20.

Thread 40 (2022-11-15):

Ball sensor

ReikoR, 2022-11-15:
For holding the balls a ball sensor should be added. Otherwise it's hard to know when the servo should be stopped.

In the lab we have IS471FE sensors and 3mm IR LEDs.

ReikoR, 2022-11-22:
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

IR LED and sensor need to be mechanically connected to thrower sides. And then wired and connected to mainboard. On the mainboard a 4-pin MicroMatch connector can be used.

ReikoR, 2022-11-25:
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

IR LED needs to be on one side of the thrower, not on the mainboard. IR sensor needs to be on the other side of the thrower. If something (like a ball) comes in between the LED and the sensor then the light will not reach the sensor and the sensor output changes, which can be detected by the microcontroller.

ReikoR, 2022-11-26:
IR LED should not be on the mainboard.
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

Closed 2022-11-27.

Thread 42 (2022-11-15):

Create Board Outline Clearance rule

ReikoR, 2022-11-15:
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

It will help with pouring the polygons:
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

Closed 2022-11-20.

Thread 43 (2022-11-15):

Use small vias

ReikoR, 2022-11-15:
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

JLCPCB minimum recommended size is 0.2/0.45 mm (0.2 mm hole, 0.45 diameter).

Smaller vias take up less space.

For higher currents it's more effective to use multiple smaller vias since via area increases faster than the current carrying capability.

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

Closed 2022-11-20.

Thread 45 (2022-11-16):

Route USB data signals as differential pair

ReikoR, 2022-11-16:
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

For more info:
https://github.com/ut-robotics/picr22-team-gibibot/issues/32

But use JLC7628 stackup instead of JLC3313 as it is cheaper.

USB differential pair trace width and spacing is different for JLC7628 stackup.

For example 8 mil (about 0.2 mm) trace space and 10.28 mil (about 0.26 mm) trace width would work:
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

ReikoR, 2022-11-20:
Values for JLC7628 stackup are not being used:
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

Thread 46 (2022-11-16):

Connect high currents with wide copper and multiple vias

ReikoR, 2022-11-16:
1. For example motor driver outputs:
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
\
You need to use direct connection for polygons in the rules and change polygon pour order from Tools -> Polygon Pours -> Polygon Manager.
\
I'm not sure if capacitor between driver outputs is of any use. It should be fine to remove it.

2. Connect GND_M pads with multiple vias.
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

3. Place capacitors below motor drivers and connect with vias. Use wide polygons on bottom layer to connect capacitors together.
Something roughly like this:
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
\
Improving motor  driver placement would probably help to simplify layout a bit.

4. Select _Pour Over All Same Net Objects_ and _Remove Dead Copper_ in Polygon Pour properties.
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

ReikoR, 2022-11-20:
1. There is no need for so many ground vias.
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

2. What is the reason/purpose of overlapping the polygons one top and bottom layers? I moved them for the picture.
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

3. Capacitors are connected to motor driver with only one via.
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

4. More vias should be connected to motor driver ground pad.
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

5. It's better to connect motor outputs with polygons.
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

6. It's better to connect thrower VCC pad with wide polygon.
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

ReikoR, 2022-11-23:
1. VCC is connected with only one via. More vias should be used for high currents.
\
Current layout:
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
\
Reverse voltage protection MOSFET could be placed on the bottom layer, connected with multiple vias to battery plus pad. Thrower plus (VCC) pad could also be connected with multiple vias.
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

2. One of the vias is cutting into motor driver output polygon.
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

3. One motor driver VM pad has 4 vias connected, others have only 2.
\
Current layout:
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
\
Proposed layout:
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

4. Smaller capacitors should be placed closest to the supply pads. 0.1uF capacitors should be the closest to motor driver VM pads.
\
Current layout:
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
\
Proposed layout:
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

5. Routing on bottom layer should be improved to avoid creating large gaps in VCC polygon. Current has to flow around those gaps.
\
Current layout (current flow marked with yellow line):
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
\
Routing mostly on top layer and moving bottom layer tracks closer to isolators should help:
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

ReikoR, 2022-11-25:
One of the capacitors (C17) is cutting into motor output polygon:
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

Closed 2022-11-26.

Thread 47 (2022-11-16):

Avoid routing ground

ReikoR, 2022-11-16:
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

Place via close to the component and connect width wide trace.

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

ReikoR, 2022-11-20:
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

Closed 2022-11-22.

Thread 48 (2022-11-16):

Improve switching regulator layout

ReikoR, 2022-11-16:
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

Try to follow _12.1 Layout Guidelines_  in [TPS62933 datasheet](https://www.ti.com/lit/ds/symlink/tps62933.pdf).

See also:
https://github.com/ut-robotics/picr22-team-owo/issues/41
https://github.com/ut-robotics/picr22-team-saga/issues/26

ReikoR, 2022-11-20:
From datasheet, section 12.1 Layout Guidelines:
> Place the inductor, input and output capacitors, and the IC on the same layer.
> Place the input and output capacitors as close as possible to the IC. The VIN and GND traces must be as wide as possible and provide sufficient vias on them to minimize trace impedance. The wide areas are also of advantage from the view point of heat dissipation.

Input and output capacitors are not on the same layer:
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

GND and VIN traces are not as wide as possible:
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

> Place a 0.1-µF ceramic decoupling capacitor or capacitors as close as possible to VIN and GND pins, which is key to EMI reduction.

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

> Keep the SW trace as physically short and wide as practical to minimize radiated emissions.

Not short and wide as possible. Inductor should be placed near SW pin.
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

ReikoR, 2022-11-23:
1. +5V feedback trace should not be routed in a big loop. In current layout it's probably better to just connect it straight from capacitors to feedback resistors on the top layer.
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

2. It would be better to connect ground with multiple vias. Moving the mounting hole would help to place input capacitors closer to the regulator.
\
Current layout:
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
\
Proposed layout:
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

3. At the output it would be better to connect 5V capacitors with a polygon. Currently 0.1uF capacitor is connected with feedback trace.
\
Current layout:
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
\
Proposed layout:
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

Closed 2022-11-25.

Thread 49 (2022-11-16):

Ignore Pad to Pad clearances within a footprint

ReikoR, 2022-11-16:
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

Closed 2022-11-20.

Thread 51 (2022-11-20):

Micromatch connectors are too close to each other

ReikoR, 2022-11-20:
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

Plugs are wider than the sockets on the board.

From [Micromatch catalog](https://www.te.com/commerce/DocumentDelivery/DDEController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) pages:

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

Closed 2022-11-22.

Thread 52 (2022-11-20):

Fix DRC errors

ReikoR, 2022-11-20:
Use **Tools -> Design Rules Check...** and fix the errors reported on the Messages panel.

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

ReikoR, 2022-11-23:
1. There is an empty text outside the board, that seems to be part of motor driver footprint. Using _Tools -> Update From PCB Libraries..._ should fix this problem.
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

2. Related to previous, the "Designator119" text should be removed from the motor driver footprint.
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

3. It's not correct to set Silk to Solder Mask Clearance to 0mm.
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
\
JLCPCB minimum recommended clearance is 0.15mm:
_The Minimum Distance Between Pad and Silkscreen is 0.15mm._
https://jlcpcb.com/capabilities/pcb-capabilities
\
Some of the problems:
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
\
Either the silkscreen on the footprint or the component placement can be adjusted to fix these problems.

Closed 2022-11-25.

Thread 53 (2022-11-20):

Avoid routing over gaps

ReikoR, 2022-11-20:
There should be reference plane (for +5V track it should be GND_M polygon on layer 2) adjacent to all signal and power connections. Typically it's a ground polygon or plane on an adjacent layer. Otherwise electromagnetic fields will spread out more and cause more noise. In a typical 4-layer stackup the layer pair 1 - 2 and 3 - 4 have small distance between them. When using one layer of a pair for reference layer and other for signal and power, the fields are more contained and less spread out, which helps with the noise.

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

Closed 2022-11-25.

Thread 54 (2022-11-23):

Prefer tented vias

ReikoR, 2022-11-23:
Untented vias can cause shorts or soldering problems in some cases.

Simplest way to use tented vias is to create new Solder Mask Expansion rule:
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

Closed 2022-11-25.

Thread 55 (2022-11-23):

Board outline

ReikoR, 2022-11-23:
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

It would be better to remove those small arcs.

ReikoR, 2022-11-25:
Board outline still needs some cleanup:
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

From https://www.altium.com/documentation/altium-designer/editing-polygonal-shaped-pcb-design-objects:
> To delete a vertex, click and hold on the vertex as if you were going to move it then press the Delete key.

Closed 2022-11-26.

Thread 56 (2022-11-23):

Routing improvements

ReikoR, 2022-11-23:
1. 3.3V tracks have inconsistent width and are the narrowest at the voltage regulator output.
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

ReikoR, 2022-11-25:
1. 5V polygon would be more useful if it was not cut by a track. Also 5V should connected first to ESD protection. Right now an additional via connects USB 5V pad straight to polygon.
\
Current layout (additional vias that should be removed marked with green):
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
\
Proposed layout (2 vias removed and tracks moved to the left):
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

Closed 2022-11-26.

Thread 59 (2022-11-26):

Some joining issue?

Akustav, 2022-11-26:
The battery boxes seem somewhat off?

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

KMKgit, 2022-11-28:
Resolved

Closed 2022-11-30.

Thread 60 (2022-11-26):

Camera location issues

Akustav, 2022-11-26:
Is it currently good that you can not see the ball in front of the robot?

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

Closed 2022-11-30.

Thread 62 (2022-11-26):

Electronics location

Akustav, 2022-11-26:
Do you have an idea of what size your electronics will be? Would be good if it is also located in the chassis.

KMKgit, 2022-11-28:
resolved

Closed 2022-11-30.

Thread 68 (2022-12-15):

What holds the ramp arms in place?

maidlam, 2022-12-15:
What are you planning to use to hold the arms in place?

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

KMKgit, 2023-01-18:
M3 bolt and 2 nuts, to get a loose fit

Closed 2023-01-18.

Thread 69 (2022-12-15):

Ramp arm can collide with motor bolt

maidlam, 2022-12-15:
The ramp arm on the motor bolts side can collide with a bolt that has an external head when the arm is in the lowest position.

This could be fixed by making the hole for a countersunk bolt.

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

maidlam, 2023-01-18:
Use 5,5 mm diameter for the countersunk holes.

KMKgit, 2023-01-19:
Done

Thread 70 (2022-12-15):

Interference between rigid ramps and top plate

maidlam, 2022-12-15:
The rigid ramps are going into the top plate.

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

Closed 2023-01-18.

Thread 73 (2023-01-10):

Mainboard documentation

ReikoR, 2023-01-10:
1.  Pinouts are missing from README.

2. Under functionality specify what input voltage and output current the motor drivers support or are configured at.

3. Under functionality specify what type of motors the board can drive.

4. BOM is not in TSV (tab-separated values, *.tsv) format.

5. Exclude components from BOM that are not an orderable parts.
\
`Kruvi_auk;Mounting hole;H1, H2, H3;3;;;`
`3x3_mm;Soldering pad;J1, J2, J3, J4, J5, J6, J16, J17, J18, J19;10;;;`

ReikoR, 2023-01-11:
1.  _"ITRIP pin is connected with 47k resistor, that sets Voltage to 2.97V"_
47k resistor sets ITRIP voltage to 2.31V.
\
_"Motor drivers have maximum limit of 35V."_
Motor driver capacitors are rated to only 25V.

2. _"3 for motor encoders (m_1; m_2; m_3) for thre DC motors"_
_"1 for Thrower motor (Viskaja) for one AC motor"_
\
Pololu motors used for wheels are brushed DC motors.
Thrower motor is brushless DC motor.
\
Encoders are not related to motor type.
DRV8243 motor driver can drive brushed DC motors.

3. "Motor drivers can be controlled through 2 PWM signals or one direction signal and one PWM signal"
\
MODE pin configuration allows only to control with 1 PWM and 1 direction signal.

4. _"Motor drivers SR pin for slew rate with 47k resistor"
"Motor drivers ITRIP pin for load current regulation with 47k resistor"
"Motor drivers IPROPI pin for driver load current analog feedback with 2.7k resistor"
"Motor drivers DIAG pin connected to MODE and GND"_
\
This is either duplicate information or does not explain the resulting configuration.

5. _"(J15) USB connection"_
\
USB connectors have standard pinout, which does not need to be documented here.

6. Typos/spelling errors
    - programmebel
    - thre
    - connecor

ReikoR, 2023-01-12:
1. _"Motor drivers have maximum limit of 25V"_
\
Motor drivers are not limited to 25V. Capacitors connected to motor drivers have voltage rating of 25V. It's safe to say that supported input voltage is up to 16.8V (4S battery), so that there is some voltage headroom.

2. _"With these drivers we can control 3 DC motors at the same time"_
\
It's important to mention which type of DC motors. Brushed or brushless.

3. _"Motor drivers SR pin for slew rate with 47k resistor to avoid PWM losses"_
\
Not sure what is meant by this.
\
From [datasheet](https://ut-robotics.github.io/picr22-home/basketball_robot_guide/electronics/drv8243-q1_datasheet_2021-08.pdf):
_"The SR pin (HW variant) or S_SR bits in the CONFIG3 register (SPI variant) determines the slew rate of the driver.
This enables the user to optimize the PWM switching losses while meeting the EM conformance requirements."_
\
Low slew rate reduces noise from switching.
High slew rate reduces switching losses and the driver heats up less.
High slew rate is better for efficiency, but highest slew rate configuration has caused problems previously.

ReikoR, 2023-01-14:
1. _"Motor drivers are not limited to 25V. Capacitors connected to motor drivers have voltage rating of 25V. It's safe to say that supported input voltage is up to 16.8V (4S lithium ion battery), so that there is some voltage headroom."_
\
You should not just copy text I wrote as an explanation.
\
Documentation should just specify the maximum voltage.
\
For example:
    * Motor driver supply up to 16.8V (4S LiPo battery). Motor driver capacitors rated for 25V.

2. _"With these drivers we can control 3 Pololu brushed DC motors at the same time"_
\
Mainboard can drive other brushed DC motors also, not just Pololu ones.

Closed 2023-01-15.

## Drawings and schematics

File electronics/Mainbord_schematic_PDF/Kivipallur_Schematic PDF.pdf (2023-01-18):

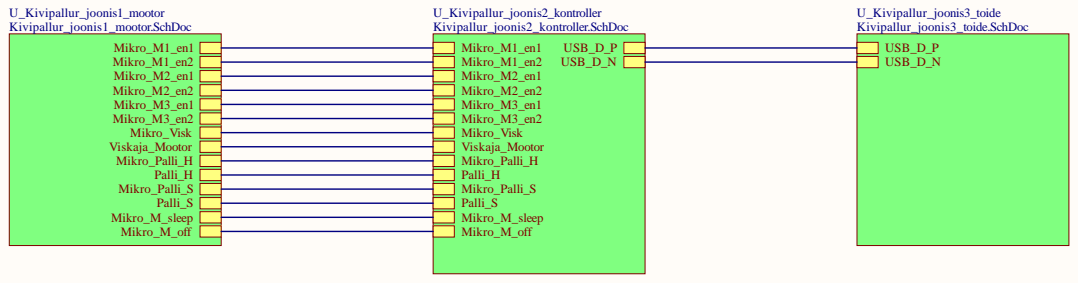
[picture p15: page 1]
Date:; Sheet of; File:; Kivipallur_joonis4.SchDoc; Drawn By:

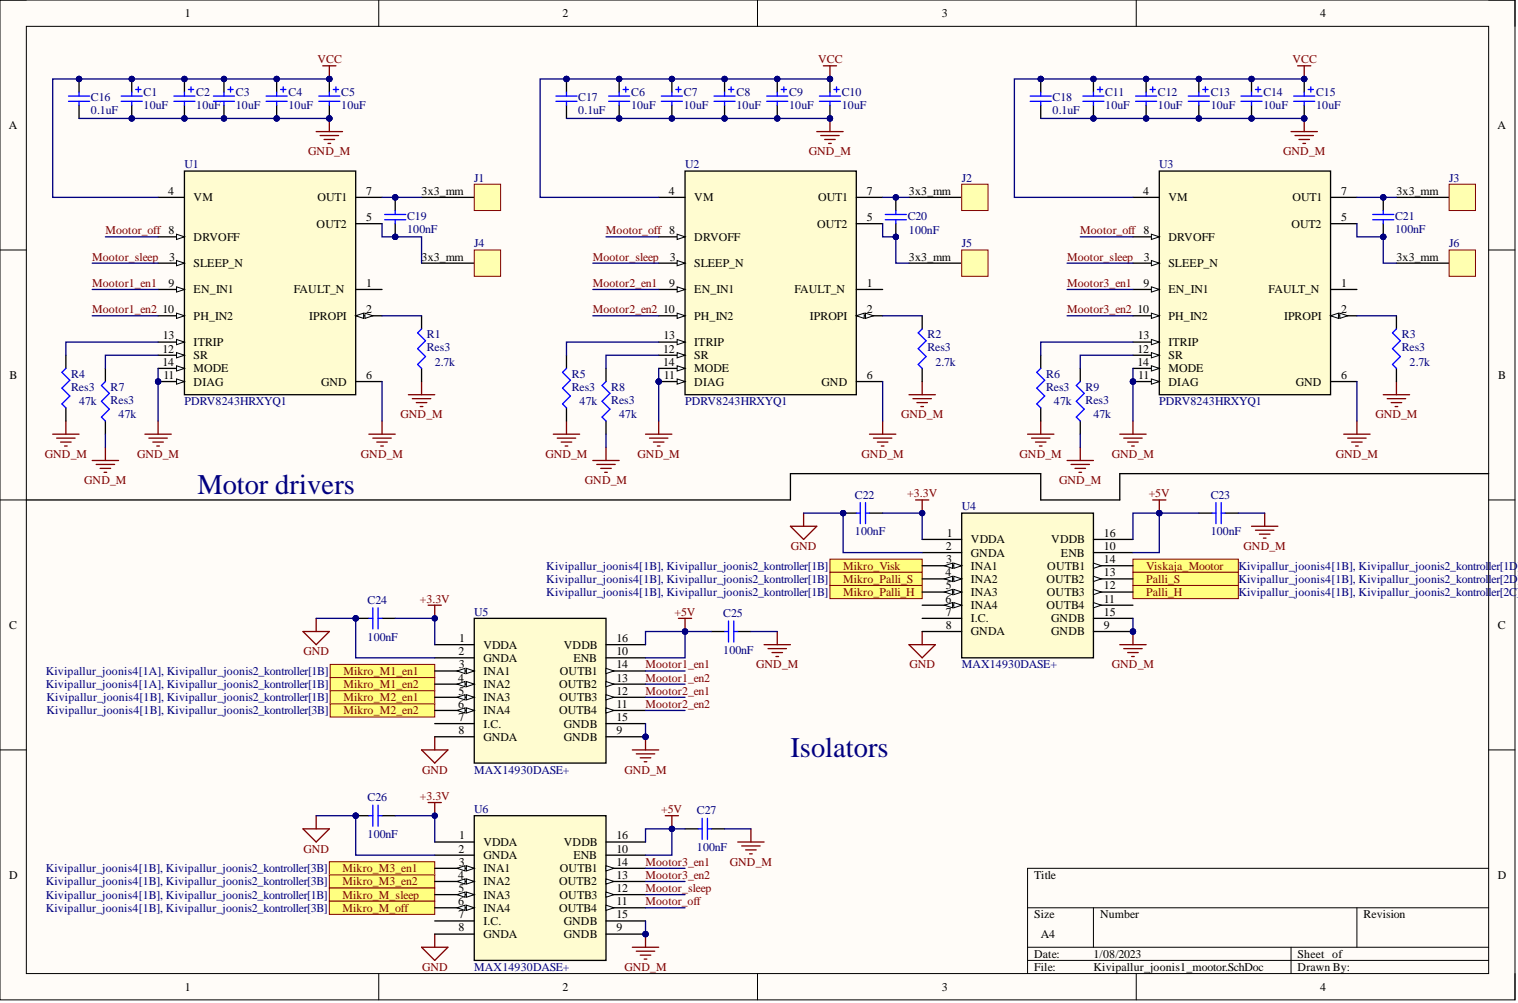
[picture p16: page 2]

INA3 5 | Mootor_sleep
INA4 6 | Mootor_off

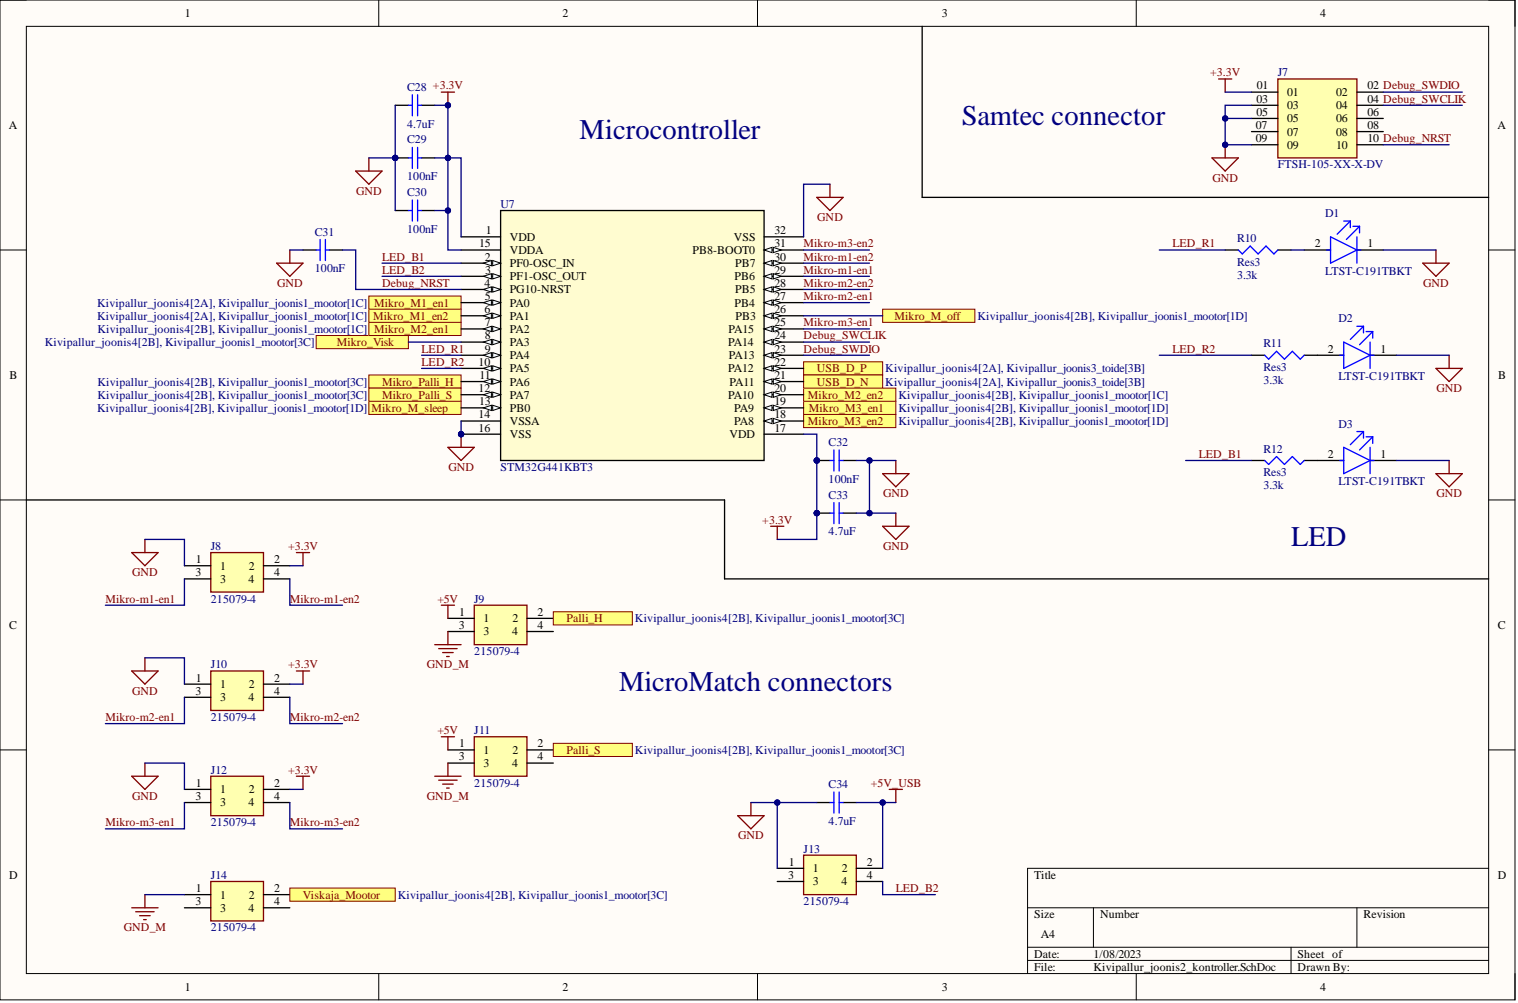
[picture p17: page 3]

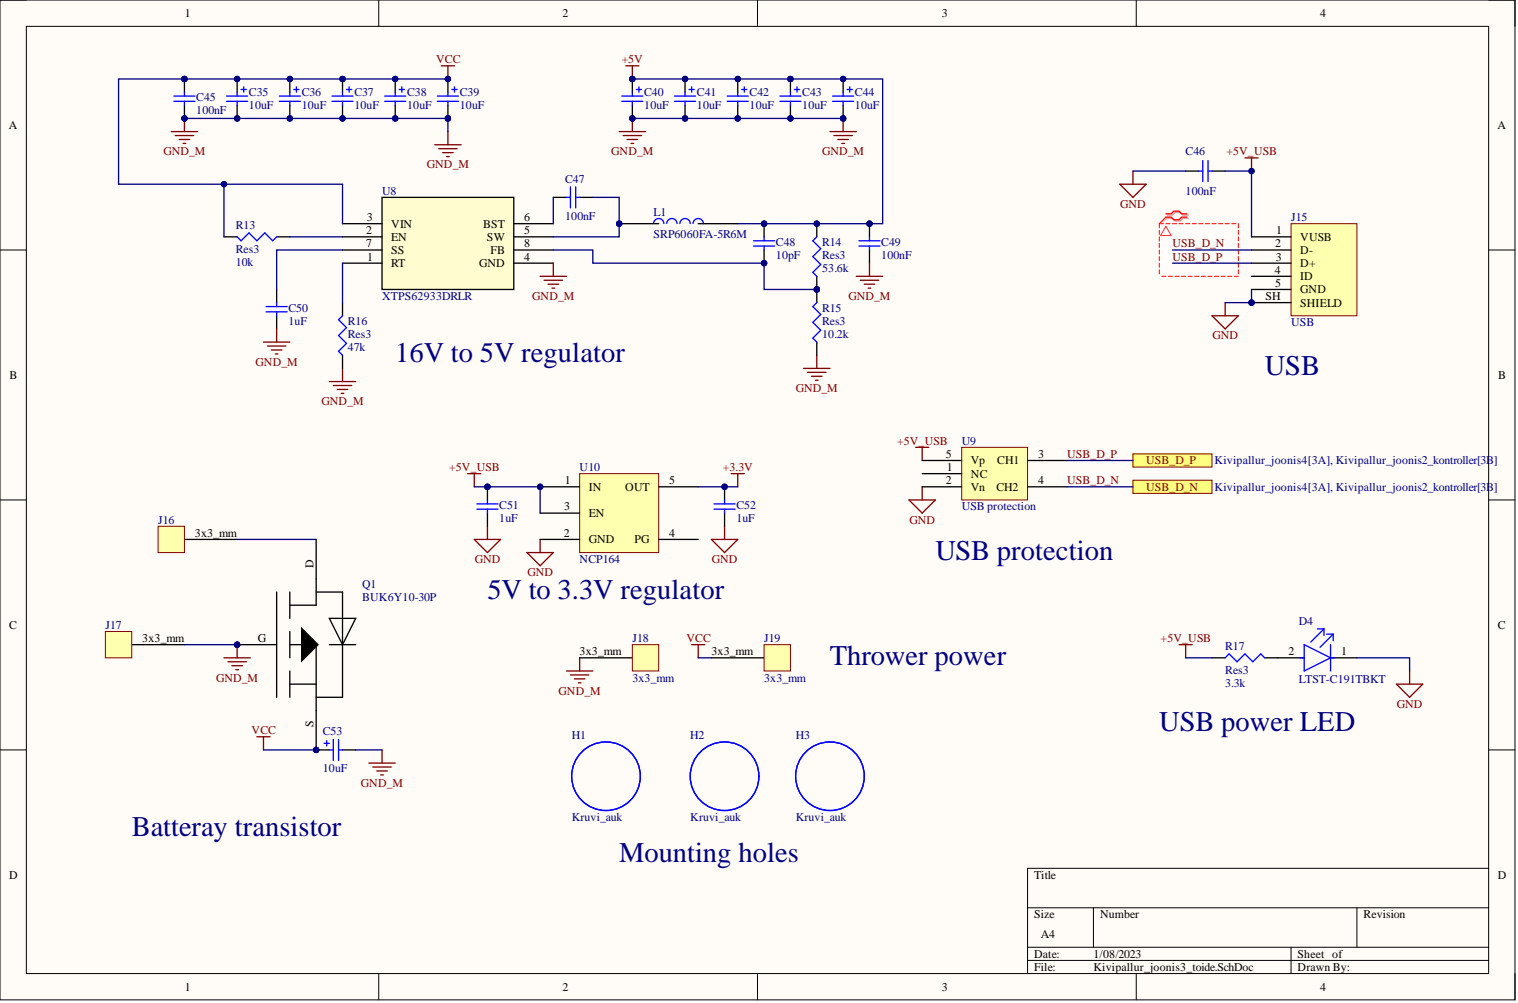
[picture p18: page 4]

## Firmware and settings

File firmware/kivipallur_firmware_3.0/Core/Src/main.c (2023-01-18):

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
/* Includes ------------------------------------------------------------------*/
#include "main.h"
#include "usb_device.h"

/* USER CODE BEGIN Includes */
#include "usbd_cdc_if.h"
/* USER CODE END Includes */

ADC_HandleTypeDef hadc1;
DMA_HandleTypeDef hdma_adc1;

CRC_HandleTypeDef hcrc;

RTC_HandleTypeDef hrtc;

TIM_HandleTypeDef htim1;
TIM_HandleTypeDef htim2;
TIM_HandleTypeDef htim3;
TIM_HandleTypeDef htim4;
TIM_HandleTypeDef htim6;
TIM_HandleTypeDef htim8;
TIM_HandleTypeDef htim15;
TIM_HandleTypeDef htim16;
TIM_HandleTypeDef htim17;

void SystemClock_Config(void);
static void MX_GPIO_Init(void);
static void MX_TIM1_Init(void);
static void MX_RTC_Init(void);
static void MX_TIM2_Init(void);
static void MX_TIM3_Init(void);
static void MX_TIM8_Init(void);
static void MX_TIM17_Init(void);
static void MX_TIM16_Init(void);
static void MX_TIM4_Init(void);
static void MX_TIM15_Init(void);
static void MX_DMA_Init(void);
static void MX_ADC1_Init(void);
static void MX_CRC_Init(void);
static void MX_TIM6_Init(void);
/* USER CODE BEGIN 0 */


typedef struct Command { // (1)
  int16_t speed1;
  int16_t speed2;
  int16_t speed3;
  uint16_t throwerSpeed;
  uint16_t delimiter; // (2)
} Command;

typedef struct Feedback { // (3)
  int16_t speed1;
  int16_t speed2;
  int16_t speed3;
  uint16_t delimiter;
} Feedback;

typedef struct MotorControl {
	int16_t speed;
	int16_t position;
	int32_t integraal;
	int16_t p_gain;
	int16_t i_gain;
	int32_t newspeed;
	int16_t positionChange;
} MotorControl;

MotorControl motor1Control = {
	  .speed = 0,
	  .position = 0,
	  .integraal = 0,
	  .p_gain = 3000,
	  .i_gain = 200,
	  .newspeed = 0,
	  .positionChange = 0
};


MotorControl motor2Control = {
	  .speed = 0,
	  .position = 0,
	  .integraal = 0,
	  .p_gain = 3000,
	  .i_gain = 200,
	  .newspeed = 0,
	  .positionChange = 0
};

MotorControl motor3Control = {
	  .speed = 0,
	  .position = 0,
	  .integraal = 0,
	  .p_gain = 3000,
	  .i_gain = 200,
	  .newspeed = 0,
	  .positionChange = 0
};


Command command = {.speed1 = 0, .speed2 = 0, .speed3 = 0, .throwerSpeed = 0, .delimiter = 0}; // (4)
volatile uint8_t isCommandReceived = 0; // (5)
uint16_t timer = 0;
uint16_t enable_pid = 0;
Feedback feedback = { // (1)
	      .speed1 = 0,
	      .speed2 = 0,
	      .speed3 = 0,
	      .delimiter = 0xAAAA
	  };;

int32_t clamp(int32_t value, int32_t minValue, int32_t maxValue) {
	if (value > maxValue) {
		return maxValue;
	}

	if (value < minValue) {
		return minValue;
	}
	return value;
}


void CDC_On_Receive(uint8_t* buffer, uint32_t* length) { // (6)
	if (*length == sizeof(Command)) { // (7)
		memcpy(&command, buffer, sizeof(Command)); // (8)

		if (command.delimiter == 0xAAAA) { // (9)
			isCommandReceived = 1;
		}
	}
}

//Näite põhjal hiljem täpsusta
// PID controller for movement.
int32_t PIDcontrol(MotorControl* control, int16_t position){
	control->positionChange = position - control->position;
	control->position = position;
	int32_t error = control->speed -control->positionChange;
	control->integraal += error;

	return control->p_gain * error + control->i_gain * control->integraal;
}

//Throw speed values
void Thrower_Send(uint16_t com) {
		if (com > 6000) {
			TIM15->CCR2 = 6000;
		}

		if (com < 20) {
			TIM15->CCR2 = 20;
		}
		TIM15->CCR2 = com;
}

void HAL_TIM_PeriodElapsedCallback(TIM_HandleTypeDef *htim6) {
	if (enable_pid == 1){

		int16_t position;
		//Mootor1
		position = (int16_t)TIM3->CNT;
		int32_t MOT_1_pwmValue = PIDcontrol(&motor1Control, position);
		HAL_GPIO_WritePin(GPIOA, MOT1_suund_Pin, (MOT_1_pwmValue < 0) ? GPIO_PIN_SET : GPIO_PIN_RESET);
		TIM1->CCR2 = (uint16_t)clamp((MOT_1_pwmValue < 0) ? -MOT_1_pwmValue : MOT_1_pwmValue, 0, 65535);

		//Mootor2
		position = (int16_t)TIM4->CNT;
		int32_t MOT_2_pwmValue = PIDcontrol(&motor2Control, position);
		HAL_GPIO_WritePin(GPIOA, MOT2_suund_Pin, (MOT_2_pwmValue < 0) ? GPIO_PIN_SET : GPIO_PIN_RESET);
		TIM2->CCR2 = (uint16_t)clamp((MOT_2_pwmValue < 0) ? -MOT_2_pwmValue : MOT_2_pwmValue, 0, 65535);

		//Mootor3
		position = (int16_t)TIM8->CNT;
		int32_t MOT_3_pwmValue = PIDcontrol(&motor3Control, position);
		HAL_GPIO_WritePin(GPIOA, MOT3_suund_Pin, (MOT_3_pwmValue < 0) ? GPIO_PIN_SET : GPIO_PIN_RESET);
		TIM2->CCR4 = (uint16_t)clamp((MOT_3_pwmValue < 0) ? -MOT_3_pwmValue : MOT_3_pwmValue, 0, 65535);

		timer+=1;
		if (timer == 50){
			timer = 0;
			enable_pid = 0;
			motor1Control.speed = 0;
			TIM1->CCR1 = 0;
			TIM1->CCR2 = 0;
			motor2Control.speed = 0;
			TIM2->CCR1 = 0;
			TIM2->CCR2 = 0;
			motor3Control.speed = 0;
			TIM2->CCR3 = 0;
			TIM2->CCR4 = 0;
			Thrower_Send(0);
		}
	}
}

//Drivers need a sleep signal to start working
void wake_drivers_up() {
	HAL_GPIO_WritePin(MOT_SLEEP_GPIO_Port, MOT_SLEEP_Pin, 0);
		for (int i = 0; i<300; i++) {
			__asm("nop");
	  	  }
	HAL_GPIO_WritePin(MOT_SLEEP_GPIO_Port, MOT_SLEEP_Pin, 1);
}
/* USER CODE END 0 */

/**
  * @brief  The application entry point.
  * @retval int
  */
int main(void)
{
  /* MCU Configuration--------------------------------------------------------*/

  /* Reset of all peripherals, Initializes the Flash interface and the Systick. */
  HAL_Init();

  /* Configure the system clock */
  SystemClock_Config();

  /* Initialize all configured peripherals */
  MX_GPIO_Init();
  MX_TIM1_Init();
  MX_RTC_Init();
  MX_TIM2_Init();
  MX_TIM3_Init();
  MX_TIM8_Init();
  MX_TIM17_Init();
  MX_TIM16_Init();
  MX_TIM4_Init();
  MX_TIM15_Init();
  MX_USB_Device_Init();
  MX_DMA_Init();
  MX_ADC1_Init();
  MX_CRC_Init();
  MX_TIM6_Init();
  /* USER CODE BEGIN 2 */

  HAL_TIM_PWM_Start(&htim15, TIM_CHANNEL_2); //Trhower

  HAL_TIM_PWM_Start(&htim1, TIM_CHANNEL_2); //Mootor1
  HAL_TIM_PWM_Start(&htim2, TIM_CHANNEL_1); //Mootor2
  HAL_TIM_PWM_Start(&htim2, TIM_CHANNEL_4); //Mootor3


  HAL_TIM_Encoder_Start(&htim3, TIM_CHANNEL_1 | TIM_CHANNEL_2);
  HAL_TIM_Encoder_Start(&htim4, TIM_CHANNEL_1 | TIM_CHANNEL_2);
  HAL_TIM_Encoder_Start(&htim8, TIM_CHANNEL_1 | TIM_CHANNEL_2);

  TIM1->CCR2 = 0;
  TIM2->CCR1 = 0;
  TIM2->CCR4 = 0;

  TIM15->CCR2 = 3000;

/*
  //for testing the motors
  TIM1->CCR1 = 0;
  TIM1->CCR2 = 20000;
  TIM2->CCR1 = 20000;
  TIM2->CCR2 = 0;
  TIM2->CCR3 = 0;
  TIM2->CCR4 = 20000;

*/


  HAL_GPIO_WritePin(MOT_SLEEP_GPIO_Port, MOT_SLEEP_Pin, 1);

  HAL_TIM_Base_Start_IT(&htim6);
  /* USER CODE END 2 */

  /* Infinite loop */
  /* USER CODE BEGIN WHILE */
  while (1) {
    /* USER CODE END WHILE */

    /* USER CODE BEGIN 3 */

	  	  if (isCommandReceived) { // (2)
	  	        isCommandReceived = 0;
	  	        wake_drivers_up();
	  	        motor1Control.speed = command.speed1;
	  	        motor2Control.speed = command.speed2;
	  	        motor3Control.speed = command.speed3;
	  	        Thrower_Send(command.throwerSpeed);
	    	        timer = 0;
	    	        enable_pid = 1;

	  	        feedback.speed1 = motor1Control.positionChange; // (4) //Mootor1
	  	        feedback.speed2 = motor2Control.positionChange;  ////Mootor2
	  	        feedback.speed3 = motor3Control.positionChange;  ////Mootor3


	  	        CDC_Transmit_FS(&feedback, sizeof(feedback)); // (5)
	  	      }
  }

}
  /* USER CODE END 3 */


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


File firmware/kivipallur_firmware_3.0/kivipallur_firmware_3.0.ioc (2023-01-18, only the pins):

Mcu.UserName=STM32G441KBTx
PA0.GPIO_Label=MOT2-PWM_1
PA0.Signal=S_TIM2_CH1
PA1.GPIO_Label=MOT2_suund
PA1.Signal=GPIO_Output
PA10.GPIO_Label=MOT3-PWM_2
PA10.Signal=S_TIM2_CH4
PA11.Signal=USB_DM
PA12.Signal=USB_DP
PA13.Signal=SYS_JTMS-SWDIO
PA14.Signal=SYS_JTCK-SWCLK
PA15.GPIO_Label=MOT3-ENC_1
PA15.Signal=S_TIM8_CH1
PA2.GPIO_Label=MOT3_suund
PA2.Signal=GPIO_Output
PA3.GPIO_Label=TRW-PWM_1
PA3.Signal=S_TIM15_CH2
PA4.GPIO_Label=LED_R1_D1
PA4.Signal=GPIO_Output
PA5.GPIO_Label=LED_R2_D2
PA5.Signal=GPXTI5
PA6.GPIO_Label=HOLD-servo_PWM
PA6.Signal=S_TIM16_CH1
PA7.GPIO_Label=AIM-servo_PWM
PA7.Signal=S_TIM17_CH1
PA8.GPIO_Label=MOT1_suund
PA8.Signal=GPIO_Output
PA9.GPIO_Label=MOT1-PWM_2
PA9.Signal=S_TIM1_CH2
PB0.GPIO_Label=MOT_SLEEP
PB0.Signal=GPIO_Output
PB3.GPIO_Label=MOT_OFF
PB3.Signal=GPIO_Output
PB4.GPIO_Label=MOT1-ENC_1
PB4.Signal=S_TIM3_CH1
PB5.GPIO_Label=MOT1-ENC_2
PB5.Signal=S_TIM3_CH2
PB6.GPIO_Label=MOT2-ENC_1
PB6.Signal=S_TIM4_CH1
PB7.GPIO_Label=MOT2-ENC_2
PB7.Signal=S_TIM4_CH2
PB8-BOOT0.GPIO_Label=MOT3-ENC_2
PB8-BOOT0.Signal=S_TIM8_CH2
PF0-OSC_IN.GPIO_Label=LED_B1_D3
PF0-OSC_IN.Signal=GPIO_Output
PF1-OSC_OUT.GPIO_Label=LED_B2
PF1-OSC_OUT.Signal=GPIO_Output

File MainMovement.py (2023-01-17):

# from logging.handlers import WatchedFileHandler
import math
from urllib import robotparser
import numpy as np
import time
import struct
import serial
import websocket
import serial.tools.list_ports as serials
from enum import Enum
from json import loads
from Color import Color
from xbox360controller import Xbox360Controller



class RobotMotion:
    wheelRadius = 0.035  
    wheelDistanceFromCenter = 0.2 
    gearboxReductionRatio = 18.75
    encoderEdgesPerMotorRevolution = 64
    pidControlFrequency = 100
    thrower_speed = 00
    wheelSpeedToMainboardUnits = gearboxReductionRatio * \
        encoderEdgesPerMotorRevolution / \
        (2 * math.pi * wheelRadius * pidControlFrequency)
    # converts wheel angles from degrees to radians
    wheelAngles = [math.radians(degree) for degree in [120, 0, 240]]
    disable_failsafe = 0

    def __init__(self):
        self.ser = None

    def open(self):
        for port in serials.comports():
            if port.vid == 1155 and port.pid == 22336:
                self.ser = serial.Serial(port.device)  # open serial port
                print("leidis seriali")
                break
        if self.ser == None:
            raise Exception("Could not establish serial connection")

    def close(self):
        print("sulgesin seriali")
        self.ser.close()

    def sendCommand(self, thrower_speed, speed1, speed2, speed3):
        self.ser.write(struct.pack('<hhhHBH', speed1, speed2, speed3, thrower_speed, self.disable_failsafe, 0xAAAA))
        # reads as many bytes as there are to read
        self.ser.read(self.ser.in_waiting)

    def move(self, x_speed, y_speed, robotAngularVelocity, thrower_speed):
        robotSpeed = math.sqrt(x_speed * x_speed + y_speed * y_speed)
        robotDirectionAngle = math.atan2(y_speed, x_speed)
        wheelSpeeds = [robotSpeed * math.cos(robotDirectionAngle - angle) +
                       self.wheelDistanceFromCenter * robotAngularVelocity for angle in self.wheelAngles]
        wheelSpeedsInMainboardUnits = [round(speed*self.wheelSpeedToMainboardUnits) for speed in wheelSpeeds]
        # thrower_speed = 0 #temporary
        # print(wheelSpeedsInMainboardUnits)
        self.sendCommand(thrower_speed, wheelSpeedsInMainboardUnits[0], wheelSpeedsInMainboardUnits[1], wheelSpeedsInMainboardUnits[2])


class States(Enum):
    spin = 0
    drive = 1
    orbit = 2
    throw = 3
    controller = 4
    enemy_basket_spin = 5
    enemy_basket_approach = 6


class StateMachine():
    def __init__(self, motion, frame_width, frame_height,):
        self.motion = motion
        self.frame_centre_x = frame_width/2
        self.frame_height = frame_height
        self.throwdist = 0
        self.throw_wo_ball = False


    def spin(self, processedData,timeoutframes):
        if timeoutframes > 500:
            return States.enemy_basket_spin

        # if it finds more than 1 ball to choose from, it goes to the drive function
        if len(processedData.balls) > 0:
            #print(processedData.balls)
            return States.drive
        else:
            # otherwise it spins until it finds some
            self.motion.move(0, 0, 1, 0)
        return States.spin

    def drive(self, processedData):
        if len(processedData.balls) > 0:
            ball = processedData.balls[-1]
            #print("distance: {}".format(ball))
            xmiddif = (self.frame_centre_x - (ball.x)) * 0.0075              #approcing ball relative to the ball's x and y coordinate
            yfor = (self.frame_height*0.75 - (ball.distance)) * 0.005
            #print("x: ", xmiddif, ", y: ", yfor)
            self.motion.move(0, yfor, xmiddif, 0)
            if ball.distance >= self.frame_height*0.73:
                # if it is close enough to a ball, it should start orbiting around it to find the basket:
                return States.orbit
            return States.drive
        # if it loses the ball for some reason (opponent takes it), it starts spinning to look for a new one:
        return States.spin
        

    def orbit(self, processedData, basketColor):
        
        basket = processedData.basket_b if basketColor == Color.BLUE else processedData.basket_m

        if len(processedData.balls) > 0 : #checks if robot can see ball
            ball = processedData.balls[-1]
            orbitrad = (self.frame_height*0.90 - ball.distance) *0.004
            orbitvar = (self.frame_centre_x - ball.x )*0.02 #variable
            
            orbitdirmultiplier = 1 #used to assign the direction of orbit
           
            pixel_difference = 3
            # if it has a basket in frame and it is centred, it goes to throw the ball:
            if basket.exists and self.frame_centre_x -pixel_difference  < basket.x < self.frame_centre_x + pixel_difference :

                print("could throw")
                return States.throw
            # if it has a ball and a basket in frame, but the basket isn't centred:
            elif basket.exists:
                orbitdirmultiplier = (self.frame_centre_x - basket.x)*0.004
                #print(orbitdirmultiplier)
                orbitdirmultiplier = max(min(orbitdirmultiplier,0.1),-0.1)

                self.motion.move(orbitdirmultiplier, orbitrad, orbitvar, 0)
                # centre basket and ball to frame
            # if it can't find a basket in the frame, it orbits faster:
            elif not basket.exists:

                self.motion.move(0.3, orbitrad, orbitvar, 0)
            return States.orbit
        # if it lost the ball, it goes to look for a new one:
        return States.spin
        


    def throw(self, processedData,basketColor):

        
        basket = processedData.basket_b if basketColor == Color.BLUE else processedData.basket_m
        thrower_speed = round(3*basket.distance) + 380 # Semi accurate thrower speed calculation based on testing
        #thrower_speed = 800
        print(basket.distance, thrower_speed, self.throw_wo_ball)

        if not self.throw_wo_ball:
            if len(processedData.balls) > 0:
                ball = processedData.balls[-1]
                xmiddif = (self.frame_centre_x*0.976 - (basket.x)) * 0.0055  #proportional driving
                
                self.motion.move(0, 0.3, xmiddif, thrower_speed) #thrower speed for revving the motor
                print(ball.distance)
                if ball.distance > 0.83*self.frame_height:        #NEEDS TUNING
                    self.throw_wo_ball = True
                    self.throwdist = basket.distance

                return States.throw
        else:
            if self.throwdist -20 < basket.distance:
                xmiddif = (self.frame_centre_x*0.976 - (basket.x)) * 0.0055  #proportional driving
                print(self.throwdist,self.throw_wo_ball)
                self.motion.move(0, 0.3, xmiddif, thrower_speed)
                return States.throw

        self.throw_wo_ball = False
        return States.spin
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

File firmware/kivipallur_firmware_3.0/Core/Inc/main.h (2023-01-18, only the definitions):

#define LED_B1_D3_Pin GPIO_PIN_0
#define LED_B1_D3_GPIO_Port GPIOF
#define LED_B2_Pin GPIO_PIN_1
#define LED_B2_GPIO_Port GPIOF
#define MOT2_PWM_1_Pin GPIO_PIN_0
#define MOT2_PWM_1_GPIO_Port GPIOA
#define MOT2_suund_Pin GPIO_PIN_1
#define MOT2_suund_GPIO_Port GPIOA
#define MOT3_suund_Pin GPIO_PIN_2
#define MOT3_suund_GPIO_Port GPIOA
#define TRW_PWM_1_Pin GPIO_PIN_3
#define TRW_PWM_1_GPIO_Port GPIOA
#define LED_R1_D1_Pin GPIO_PIN_4
#define LED_R1_D1_GPIO_Port GPIOA
#define LED_R2_D2_Pin GPIO_PIN_5
#define LED_R2_D2_GPIO_Port GPIOA
#define LED_R2_D2_EXTI_IRQn EXTI9_5_IRQn
#define HOLD_servo_PWM_Pin GPIO_PIN_6
#define HOLD_servo_PWM_GPIO_Port GPIOA
#define AIM_servo_PWM_Pin GPIO_PIN_7
#define AIM_servo_PWM_GPIO_Port GPIOA
#define MOT_SLEEP_Pin GPIO_PIN_0
#define MOT_SLEEP_GPIO_Port GPIOB
#define MOT1_suund_Pin GPIO_PIN_8
#define MOT1_suund_GPIO_Port GPIOA
#define MOT1_PWM_2_Pin GPIO_PIN_9
#define MOT1_PWM_2_GPIO_Port GPIOA
#define MOT3_PWM_2_Pin GPIO_PIN_10
#define MOT3_PWM_2_GPIO_Port GPIOA
#define MOT3_ENC_1_Pin GPIO_PIN_15
#define MOT3_ENC_1_GPIO_Port GPIOA
#define MOT_OFF_Pin GPIO_PIN_3
#define MOT_OFF_GPIO_Port GPIOB
#define MOT1_ENC_1_Pin GPIO_PIN_4
#define MOT1_ENC_1_GPIO_Port GPIOB
#define MOT1_ENC_2_Pin GPIO_PIN_5
#define MOT1_ENC_2_GPIO_Port GPIOB
#define MOT2_ENC_1_Pin GPIO_PIN_6
#define MOT2_ENC_1_GPIO_Port GPIOB
#define MOT2_ENC_2_Pin GPIO_PIN_7
#define MOT2_ENC_2_GPIO_Port GPIOB
#define MOT3_ENC_2_Pin GPIO_PIN_8
#define MOT3_ENC_2_GPIO_Port GPIOB

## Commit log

2022-09-12 Update MainboardCommunication.py
    eemaldasin testi printimised
2022-09-23 Update README.asciidoc
    fixed external links title just in case we might lose any points
2022-10-30 Praegusrks olemas olevad failid
    [21-0041_S16+1_MXM.step, 21-0041_S161_MXM.step, 3x3_mm.PcbLib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]
2022-10-30 failid ühte kausta
    [Kivipallur.PrjPcb, Kivipallur_joonis1.SchDoc, Kivipallur_joonis2.SchDoc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]
2022-10-30 eemalda ajalugu
    [MAX14930DASE&plus_.SchLib]
2022-11-06 skeemi parandused
    [Kivipallur.PrjPcb, Kivipallur_joonis1.SchDoc, Kivipallur_joonis2.SchDoc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]
2022-11-07 Add files via upload
    failid
    [MainMovement.py, camera.py, config_colors.py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]
2022-11-12 parandused skeemil
    [Kivipallur_joonis3.SchDoc, Kivipallur_plaat.PcbDoc]
2022-11-21 Räägitud parandused
    [21-0041_S16+1_MXM.step, 21-0041_S161_MXM.step, 3x3_mm.PcbLib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]
2022-11-22 põhjad korras
    [3mm IR LED.PcbLib, 3mm IR LED.SchLib, IS471FE.PcbLib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]
2022-11-26 Gerber x2
    [Kivipallur.PrjPcb, Kivipallur_joonis2_kontroller.SchDoc, Kivipallur_joonis3_toide.SchDoc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]
2022-11-27 veel faile gerber
    [Kivipallur_plaat_Copper_Signal_1.gbr, Kivipallur_plaat_Copper_Signal_2.gbr, Kivipallur_plaat_Copper_Signal_Bot.gbr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]
2022-12-15 Fixed small issues improved throwing
    [MainMovement.py, camera.py, image_processor.py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]
2023-01-08 BOM test
    [Kivipallur_BOM.csv, Kivipallur_BOM.xlsx]
2023-01-11 dokumentatsioon parandus
    [Kivipallur_BOM.csv, Kivipallur_BOM.xlsx]
2023-01-11 tühikud
    [Kivipallur_BOM.csv, Kivipallur_BOM.xlsx]
2023-01-12 uus V
    [Kivipallur_BOM.tsv]
2023-01-12 12.01 parandused
    [Kivipallur_BOM.tsv]
2023-01-15 uus komponendi kood
    [Kivipallur_BOM.tsv]

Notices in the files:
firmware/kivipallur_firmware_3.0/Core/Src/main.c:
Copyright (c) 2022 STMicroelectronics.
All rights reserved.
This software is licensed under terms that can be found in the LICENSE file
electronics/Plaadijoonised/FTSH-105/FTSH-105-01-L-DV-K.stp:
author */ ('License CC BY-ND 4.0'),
